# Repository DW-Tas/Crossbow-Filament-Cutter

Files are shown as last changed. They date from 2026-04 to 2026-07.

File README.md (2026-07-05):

[][cc-by-nc-sa]

# Crossbow
### A CNC filament cutter from DW-Tas: <a href="https://ko-fi.com/O5O5OCC0K"> Ko-Fi</a>, <a href="https://github.com/DW-Tas">GitHub</a>

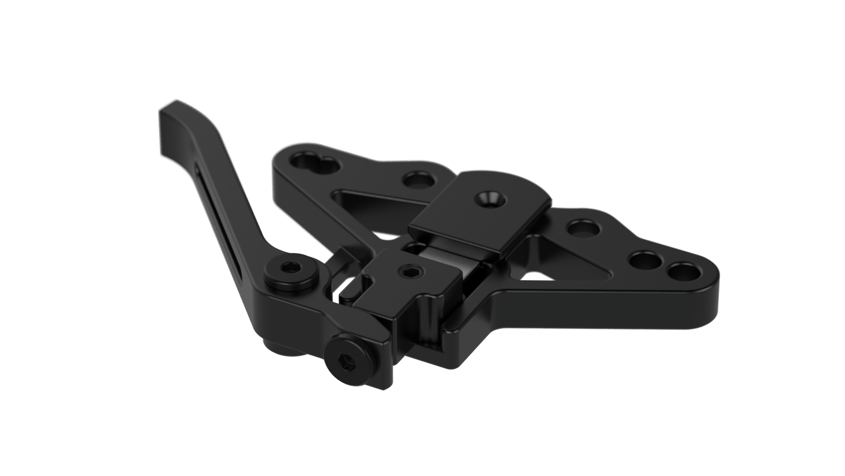
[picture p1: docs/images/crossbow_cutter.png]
<br/>

## Design philosophy
The crossbow filament cutter was developed to provide a robust, reliable, easily serviceable, versatile and universal filament cutting solution for printed toolheads. Key features include:
1. Aluminum CNC construction: Reliable cutting action that can withstand multi-thousand operations without wear.
2. Low profile and low mass: maintains toolhead rigidity, centre of mass and input shaper performance.
3. Ease of servicing: two easily accessible screws to remove and replace cutting blade and clean the filament path.

## Designed for the A4T, but intended for universal use
Crossbow was designed and developed around the A4T, but is intended for universal for use in printed toolheads that have a flat mounting surface below the extruder.<br/><br/>
Crossbow A4T parts can be downloaded here: <a href="https://github.com/Armchair-Heavy-Industries/A4T/tree/main/STL/Extruder%20Adapters/For%20Crossbow%20filament%20cutter">https://github.com/Armchair-Heavy-Industries/A4T</a>.
<br/><br/>

> [!TIP] 
> The design accomodates extruders that use the Sherpa-Mini or Oribiter v2.0 mounting hole spacing (Checked for fit with Dragon Burner in CAD models with an example Dragon Burner Mod included in the [Dragon Burner example](<Dragon Burner example>) folder).<br/><br/>

## Blade replacement
Blade replacement is generally recomended after 3000-4000 cuts, depending on the material being cut. Crossbow can use a #17A or #4 hobby knife blade. Trimming the blades to size is required. The following jig is available to help cut the blade down.

**Jig BOM:**
1. 4x M3x8 SHCS / BHCS screws
2. 4x M3 Square Nuts (DIN 562)
3. #17 or #4 hobby knife blade
4. Printed jig parts: [Blade cutting and alignment jig.stl](<STL/Blade cutting and alignment jig.stl>)

**Instructions video:**<br/>
[](https://www.youtube.com/embed/HI4ksrRDHjI)

<br/><br/>

## Screw adjustment

> [!WARNING] 
> The two main screws that act as pivots should have medium thread locking compound applied.

* **Lever Arm Pivot:** Tighten the screw to allow smooth movement of the lever arm during cutting, while preventing vertical play or rattling.
* **Blade Holder Pivot:** Start with the screw too loose then tighten the screw until the blade begins to shift slightly toward the filament path during its cutting motion. This ensures full travel of the cutting arm and minimizes unwanted movement.

<br/><br/>

## Metal top cap

> [!WARNING] 
> There is a small metal piece in the kit that is a top cap that sits above the blade.

Install it into the printed part that holds the Crossbow between your extruder and toolhead.<br>
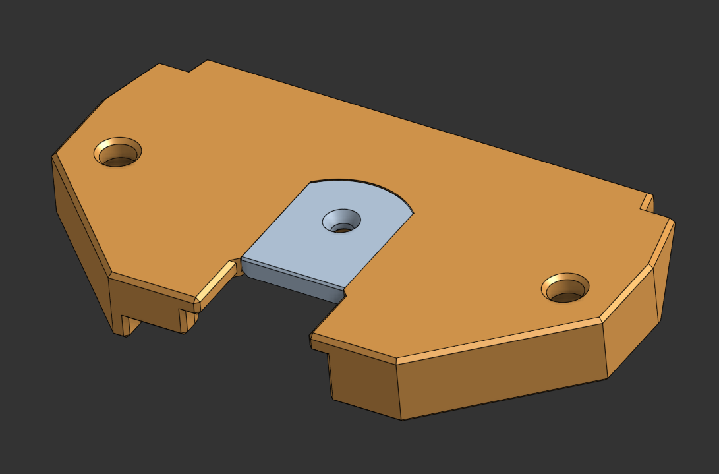
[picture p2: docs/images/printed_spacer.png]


<br><br>

## Licenced manufacturers
Crossbow is being manufactured under license by:<br/>

| Manufacturer | Purchase Link |
| --- | --- |
| Fysetc <br/> <center>Fysetc</center> | https://aliexpress.com/item/1005009769281594.html |
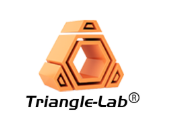
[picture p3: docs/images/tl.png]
|  | https://aliexpress.com/item/1005011557554076.html |
|  | https://aliexpress.com/item/1005011575849723.html |

<br/><br/>
> [!TIP] 
> ### You can help support the development of this project.<br/>
> Donate at https://ko-fi.com/dwtas<br/>
ko-fi (https://ko-fi.com/dwtas)
<br/><br/>

### Credits
* Inspired by Treintjes' <a href="https://github.com/Treintjes/Magneto_Filament_Cutter">Magneto_Filament_Cutter</a><br/><br/>
* Beta testers
  * igiannakas <a href="https://github.com/igiannakas/">GitHub</a>
  * KnightRadiant <a href="https://github.com/jrlomas/">GitHub</a>
  * jeremytodd1
  * jbob
<br/><br/>
#### This work is licensed under a
[Creative Commons Attribution-NonCommercial-ShareAlike 4.0 International License][cc-by-nc-sa].

[][cc-by-nc-sa]

[cc-by-nc-sa]: http://creativecommons.org/licenses/by-nc-sa/4.0/
[cc-by-nc-sa-image]: https://licensebuttons.net/l/by-nc-sa/4.0/88x31.png
[cc-by-nc-sa-shield]: https://img.shields.io/badge/License-CC%20BY--NC--SA%204.0-lightgrey.svg

### License clarification regarding non-commercial use:
The non-commercial aspect of this license is for cases where Crossbow is the product, not the use of Crossbow to create products.<br/>
I.e. If you wish to sell Crossbow as a product, you would need to seek a commercial license before doing so. </br>
It is NOT intended to prevent the use of Crossbow in a printer that you use to provide commercial services. If you want to run Crossbow as a toolhead for your print farm printers, go right ahead.

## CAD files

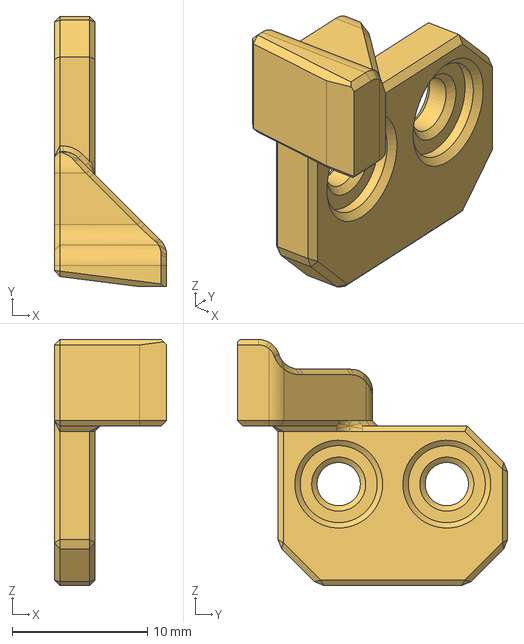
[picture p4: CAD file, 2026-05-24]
CAD/Crossbow Depressor Arm [Voron v0.2].step
8.30 x 20.0 x 18.2 mm

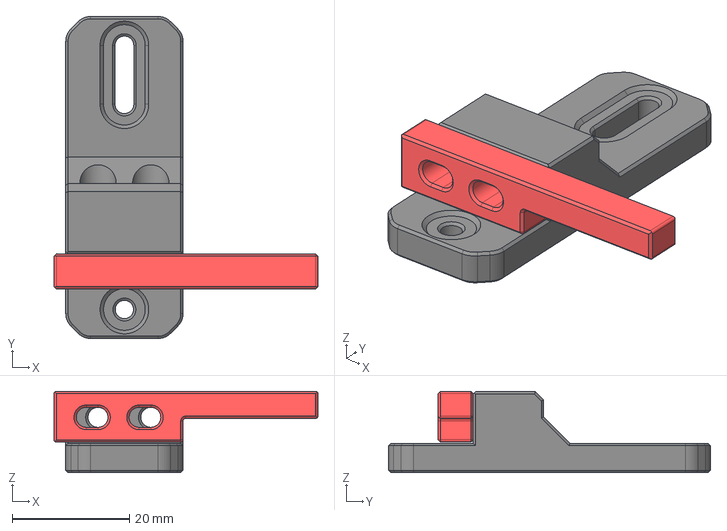
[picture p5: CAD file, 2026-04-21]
CAD/Crossbow Depressor Arm and Holder [Standard Voron Gantry].step
45.0 x 54.9 x 13.9 mm
Depressor Arm Base
Depressor Arm

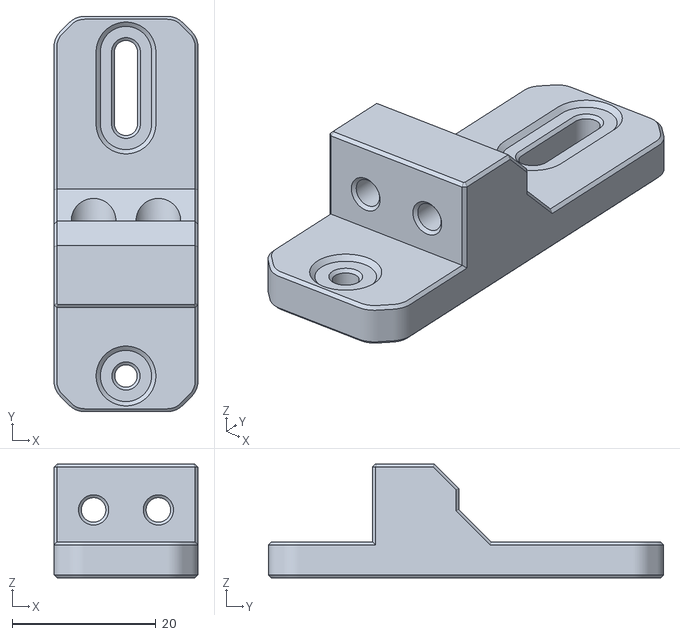
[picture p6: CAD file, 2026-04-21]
STL/Depressor Assemblies/Depressor Arm Base [Monolith Gantry].stl
20.0 x 54.9 x 15.8

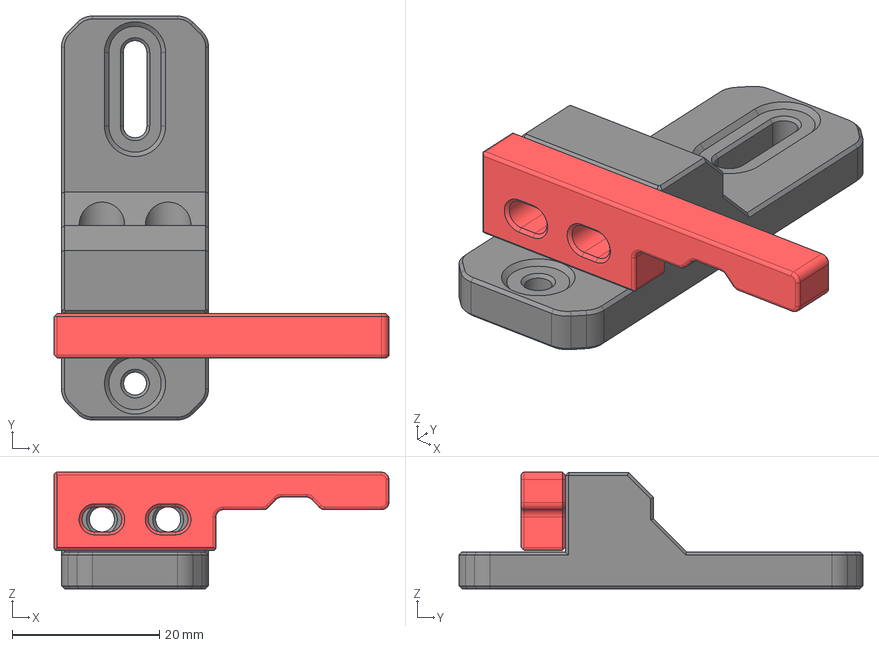
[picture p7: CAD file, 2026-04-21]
CAD/Crossbow Depressor Arm and Holder [Monolith Gantry].step
45.5 x 54.9 x 15.8 mm
Depressor Arm Base
Depressor Arm

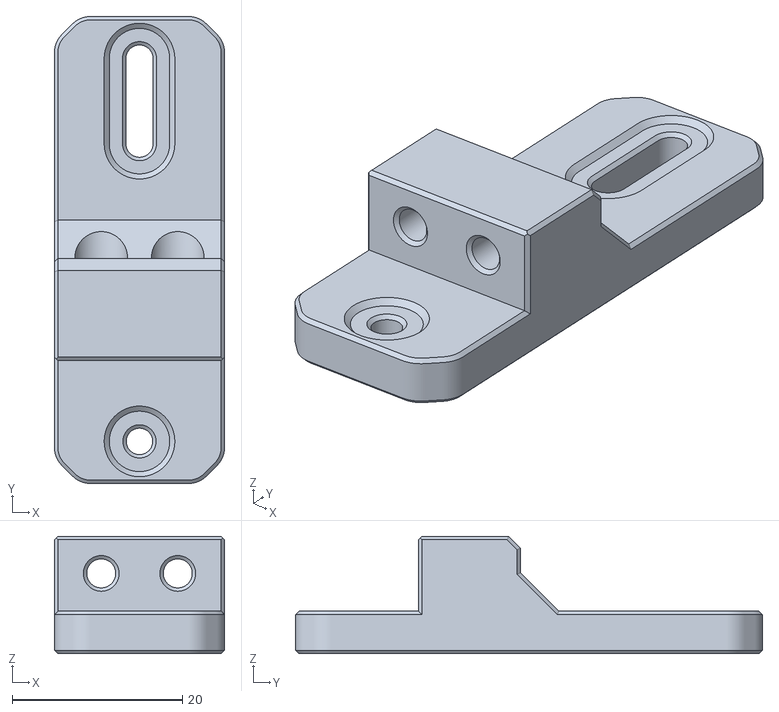
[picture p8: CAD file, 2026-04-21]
STL/Depressor Assemblies/Depressor Arm Base [Standard Gantry].stl
20.0 x 54.9 x 13.8

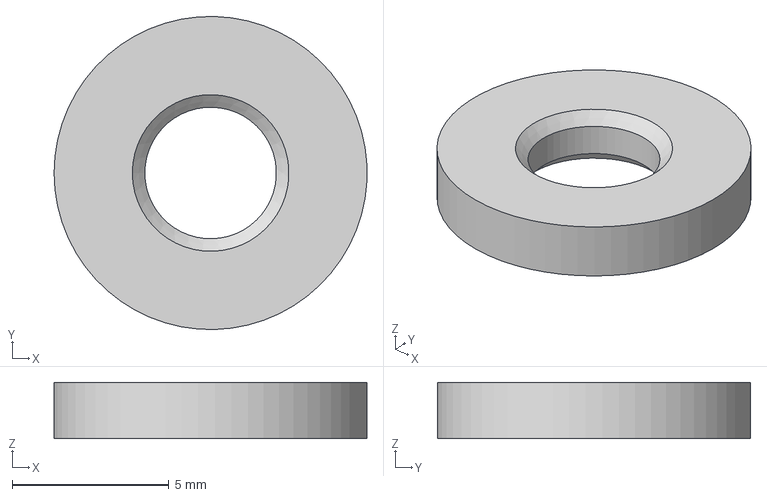
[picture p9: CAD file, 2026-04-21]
CAD/PTFE tube cutter jig.step
9.99 x 10.00 x 1.80 mm

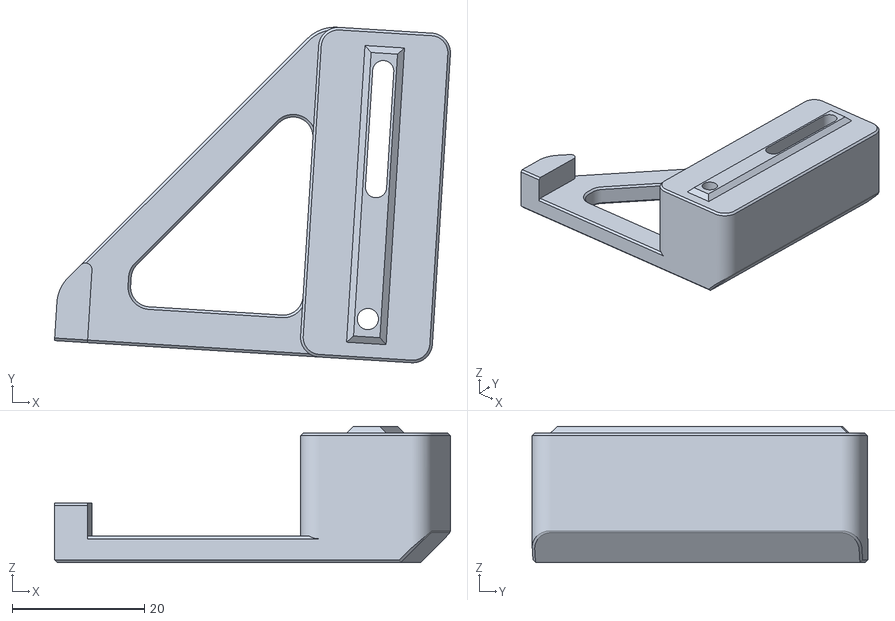
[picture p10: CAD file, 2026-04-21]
STL/Depressor Assemblies/Depressor [Siboor trident 9mm].stl
59.9 x 50.8 x 20.6

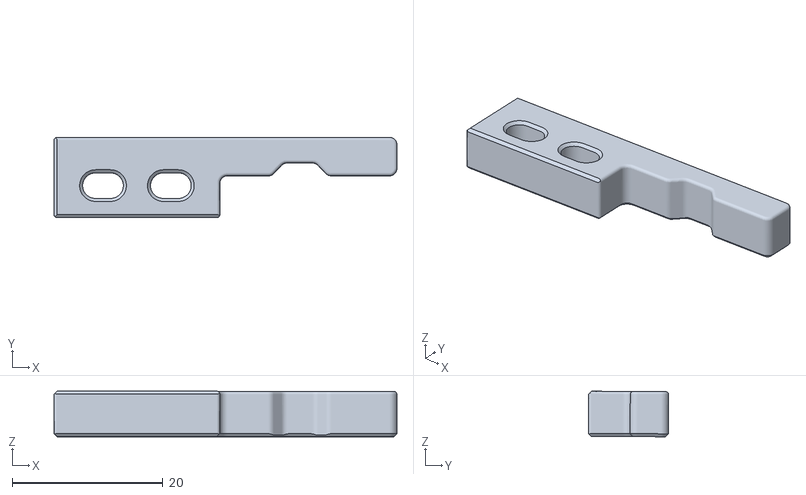
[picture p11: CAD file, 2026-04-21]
STL/Depressor Assemblies/Depressor Arm [Monolith Gantry].stl
45.5 x 10.7 x 6.05

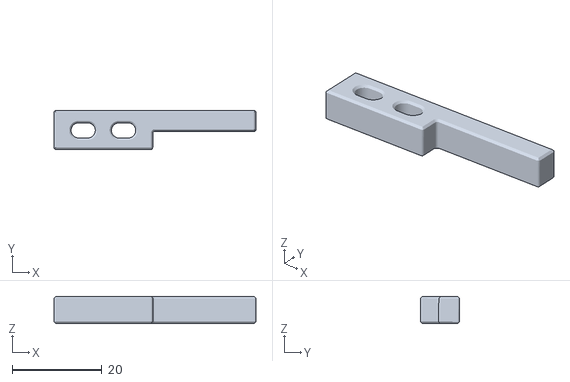
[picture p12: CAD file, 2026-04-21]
STL/Depressor Assemblies/Depressor Arm [Standard Voron Gantry].stl
45.0 x 8.71 x 6.05

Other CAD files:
STL/Depressor Assemblies/Crossbow Depressor Arm [Voron V0.2].stl
STL/PTFE tube cutter jig.stl

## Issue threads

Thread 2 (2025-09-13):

Request for a slight design change

VIN-y, 2025-09-13:
Hi,

I am Vin, the creator of MissChanger a tool-changer for Voron printers.

For the next version of MissChanger (MCv2), I am looking to add support for the Crossbow Filament Cutter (CFC). However, early prototypes had shown some problem with the default set-up of the CFC. As the cutting force act to push the tool-head away from the x-gantry, it induces a lot of stress on the tool-change mechanism on the x-carriage, pulling the layers on apart. This problem will most likely effect the 3D-printed version of the Stealthchanger / Tapchanger / etc.

With that in mind, I would like to propose that the gap in the lever arm of the cutter be widen slightly, such that the M3 bolt can pass through. This will allow the use of the configuration in the picture below. As it is, I have to slightly file away some material away, also see below.

Best regards,
VIN

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

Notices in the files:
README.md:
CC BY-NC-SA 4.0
